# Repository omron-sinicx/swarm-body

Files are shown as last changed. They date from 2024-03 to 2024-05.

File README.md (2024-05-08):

# maru: a miniature-sized wheeled robot for swarm robotics research

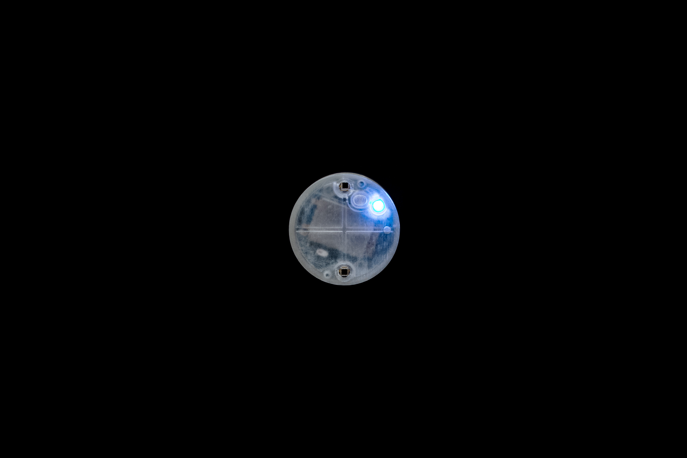
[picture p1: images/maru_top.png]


"maru" (= *miniature assemblage adaptive robot unit*) is a custom-made, miniature-sized, two-wheeled robot designed specifically for tabletop swarm robotics research.
This platform enables researchers and hobbyists to explore the dynamics of swarm robotics in a controlled, tabletop environment.

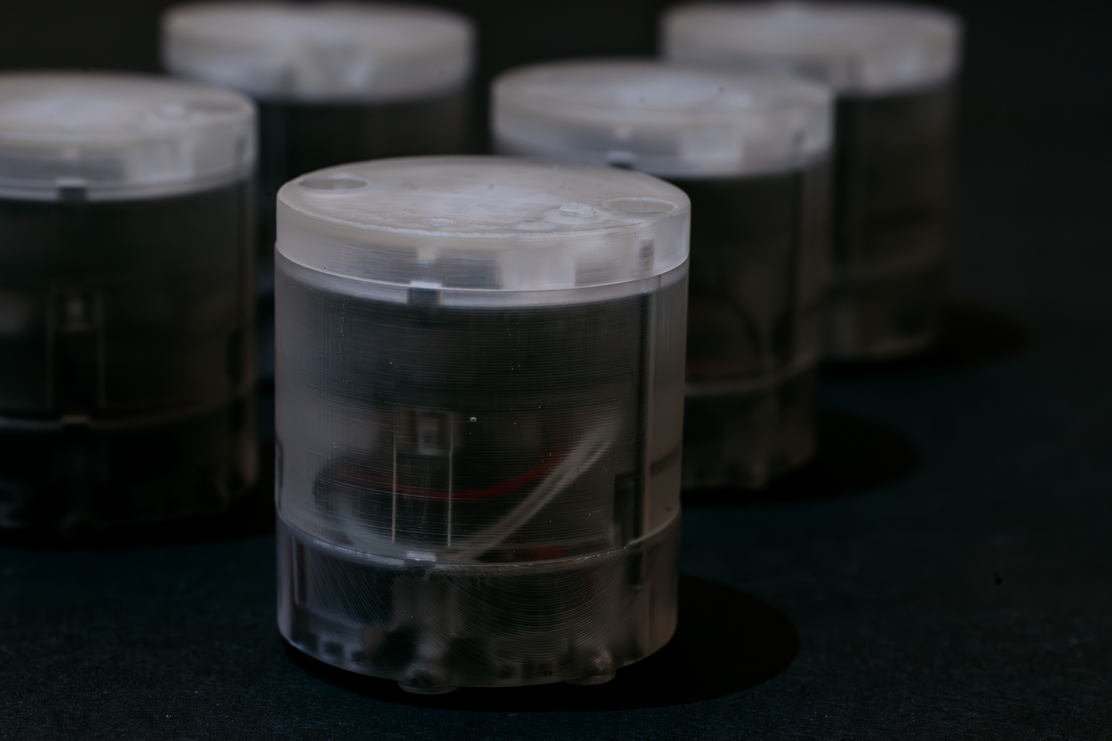
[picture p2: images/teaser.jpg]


This repository serves as a comprehensive resource for assembling and operating maru, providing detailed documentation and files, including:

- `hardware/3Dmodel` 3D models of the robot and its cradle (a combined communication and charging module),
- `hardware/circuit/schematic` Circuit schematics to guide the electronic assembly,
- `hardware/circuit/gerber` Gerber files for PCB manufacturing,
- `software/firmware` Firmware for both the robot and the cradle, distributed in binary format (Note: There are currently no plans to release the source code),
- `software/control` APIs and sample codes to help you get started with programming the robot for various tasks and behaviors (C# and Python).

This project draws inspiration from [Zooids](https://github.com/ShapeLab/SwarmUI), an open-source swarm robot platform.
Similar to Zooids, maru employs projection-based position tracking; however both maru's hardware and software are entirely new designs, another platform for swarm robotics research in HCI.

## Hardware
<!-- ![](./images/size.png) -->
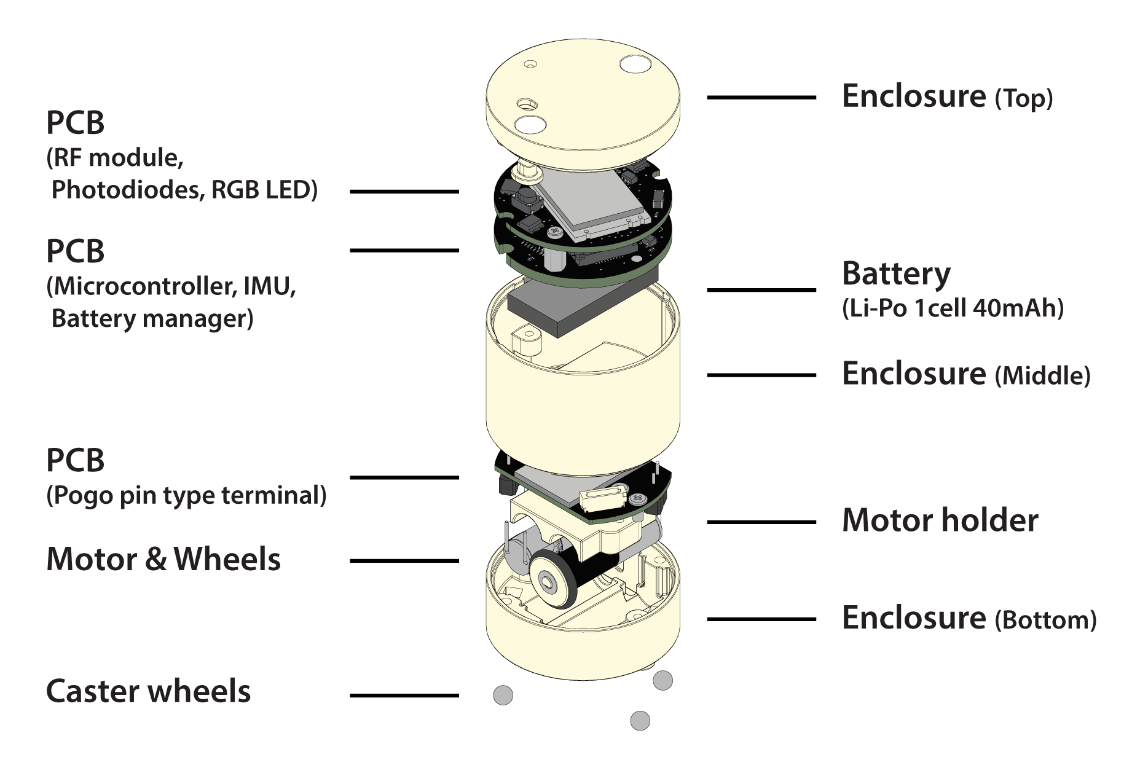
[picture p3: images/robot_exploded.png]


The hardware design is shown above.
The dimensions are 30 mm in diameter and 34 mm in height, weighing about 23 g.
The robot parts include a microcontroller unit (STM32G071KBU62 from STMicroelectronics), motor drivers (DRV8837DSGR3 from Texas Instruments), RF module (RF2401F204 from NiceRF), motors with a 26:1 planetary gearbox (Pololu 23575), photodiode (PD15-22C/TR86 from Everlight Electronics), and a 40mAh Li-Po battery.

Since the robot is lightweight, the robot may fall over while moving if the moving speed is too fast.
Magnets can be attached to the bottom of the robot, and the robot can be run on steel or other materials to keep it from falling over.

A detailed description of the hardware design and specifications is available [here](https://shigeodayo.notion.site/Hardware-Manual-8442a3ade0ba457dba1eb5f8b898ae2d?pvs=4).

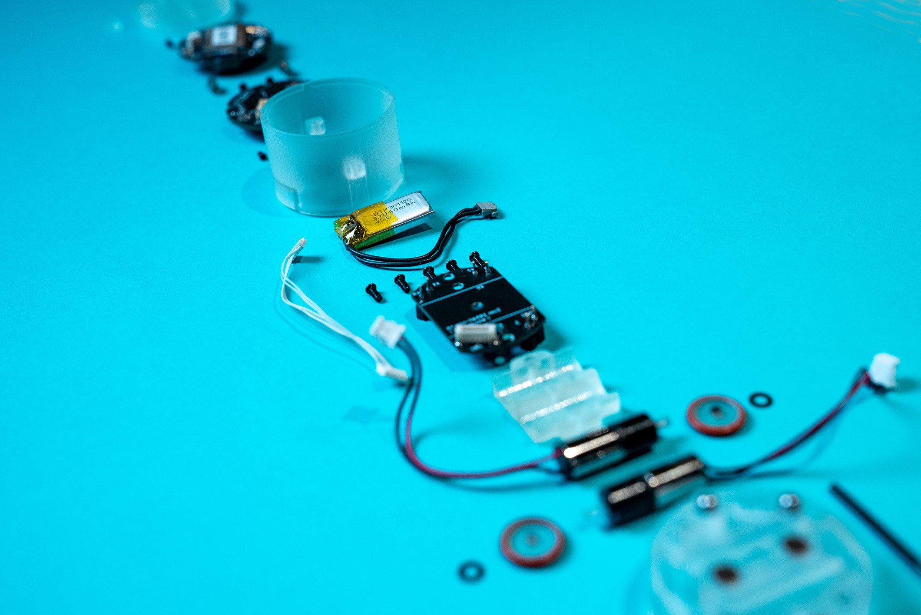
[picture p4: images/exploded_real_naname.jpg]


## Software

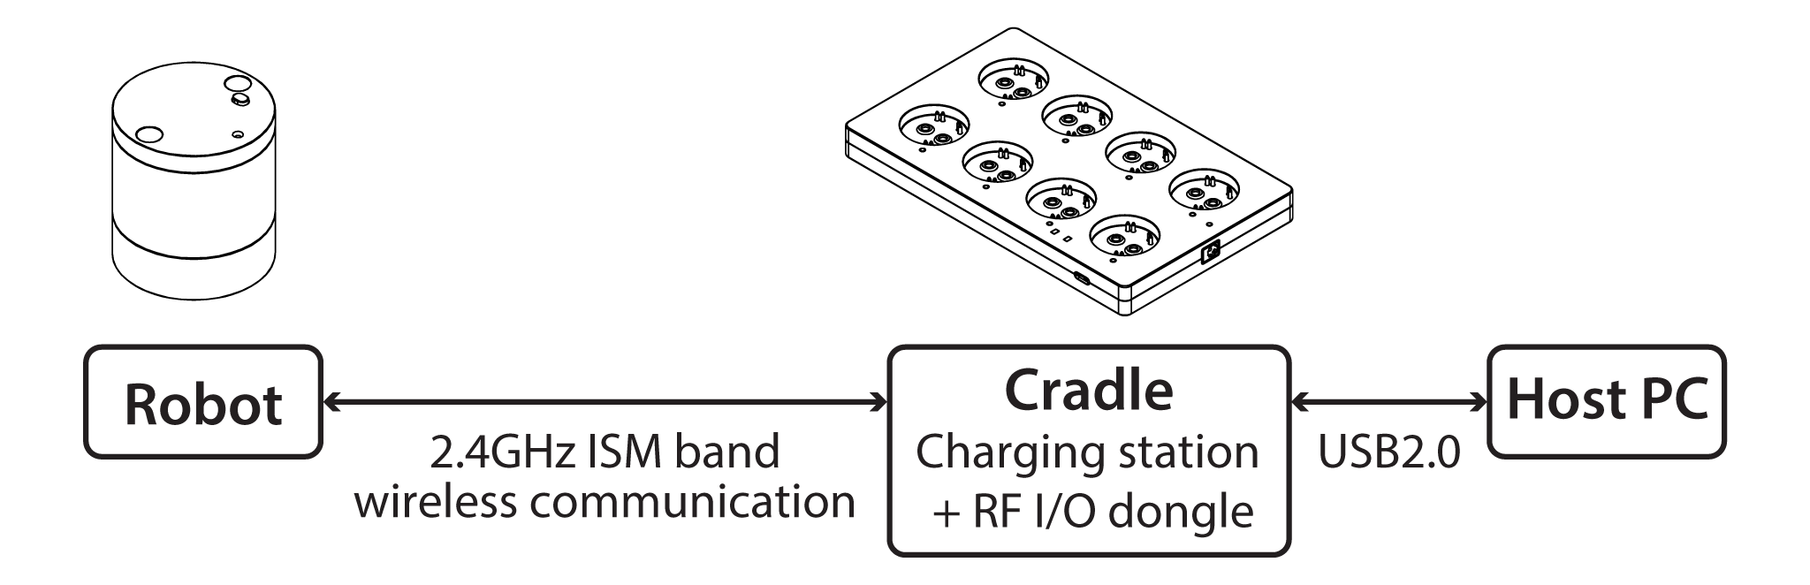
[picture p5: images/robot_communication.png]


The communication between the robots and the host computer is shown above.
The robots and the cradles (charging station + RF/IO dongle) are each equipped with an RF module and communicate through a 2.4GHz ISM band wireless communication.
The user does not need to be aware of the communication control between the robot and the cradles, as it is performed on the firmware of both devices.
The user can easily control the robot wirelessly by sending the specified commands.

A detailed description of the software design and specifications is available [here](https://shigeodayo.notion.site/Software-Manual-53adfd3b5a8c482b9a2acadc83991381?pvs=4).

## Projection-based Localization
A projection-based localization system used for the Zooids was used to track the robots.
A high-speed projector (DLP LightCrafter 45007 from Texas Instruments) was used to project a sequence of gray-coded patterns onto the table; the two photodiodes on the robot received the projected coded-pattern light, and the microcontroller of the robot decoded its pattern into position information.
Then, the robot calculated its orientation from the positions of two photodiodes and broadcasted its position and orientation information to the host computer.

For instructions on the projector tracking system, see https://github.com/ShapeLab/SwarmUI/tree/master/Hardware/Projector%20Tracking%20Setup

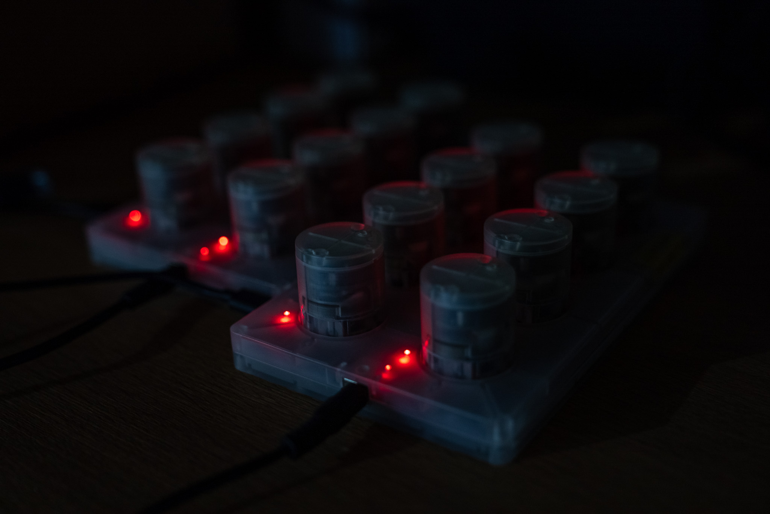
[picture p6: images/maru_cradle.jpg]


## Note

This is a joint work between [OMRON SINIC X Corporation](https://www.omron.com/sinicx/), [Cluster Metaverse Lab](https://lab.cluster.mu/en/), and [karakuri products, inc](https://krkrpro.com).

If you prefer purchasing pre-assembled robots instead of assembling them yourself, please contact [karakuri products, inc](https://krkrpro.com).

## Lisence

The software materials of this project are under an MIT license.

The hardware materials of this project are under a [Creative Commons Attribution 4.0 International License](https://creativecommons.org/licenses/by/4.0/).

## Paper
This robot was first introduced and used in the following paper:

Sosuke Ichihashi, So Kuroki, Mai Nishimura, Kazumi Kasaura, Takefumi Hiraki, Kazutoshi Tanaka, and Shigeo Yoshida. 2024. Swarm Body: Embodied Swarm Robots. In Proceedings of the CHI Conference on Human Factors in Computing Systems (CHI ’24), May 11–16, 2024, Honolulu, HI, USA. ACM, New York, NY, USA, 19 pages. https://doi.org/10.1145/3613904.3642870

```
@inproceedings{ichihashi2024swarm,
  author = {Ichihashi, Sosuke and Kuroki, So and Nishimura, Mai and Kasaura, Kazumi and Hiraki, Takefumi and Tanaka, Kazutoshi and Yoshida, Shigeo},
  title = {Swarm Body: Embodied Swarm Robots},
  year = {2024},
  publisher = {Association for Computing Machinery},
  address = {New York, NY, USA},
  url = {[https://doi.org/10.1145/3613904.3642870](https://doi.org/10.1145/3613904.3642870)},
  doi = {10.1145/3613904.3642870},
  booktitle = {Proceedings of the 2024 CHI Conference on Human Factors in Computing Systems},
  numpages = {19},
  location = {, Honolulu, HI, USA, },
  series = {CHI '24}
}
```

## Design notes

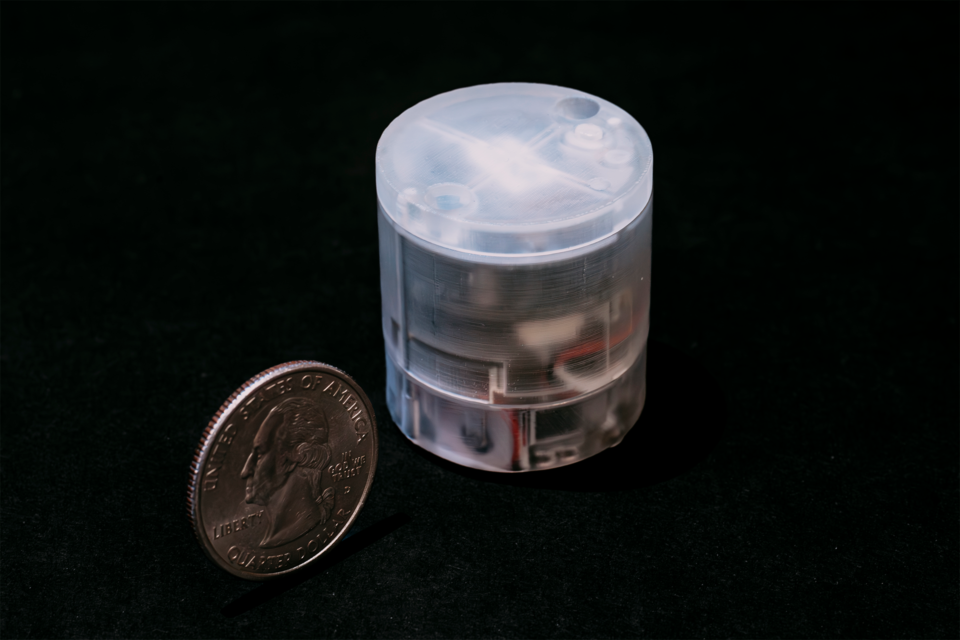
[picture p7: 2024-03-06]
images/size.png

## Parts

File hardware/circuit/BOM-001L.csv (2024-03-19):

Item | Quantity | Designator | Value | Description | Manufacturer | Manufacturer Part Number | Digikey Part Number
1 | 8 | C1, C2, C5, C15, C19, C20, C21, C37 | 0.1μF | CAP CER 0.1UF 10V X5R 0402 | Murata Electronics | GRM155R61A104KA01D | 490-1318-1-ND
2 | 3 | C3, C13, C14 | 1μF | CAP CER 1UF 10V X6S 0402 | Murata Electronics | GRM155C81A105KA12D | 490-12699-1-ND
3 | 1 | C4 | 0.47μF | CAP CER 0.47UF 10V X5R 0402 | Murata Electronics | GRM155R61A474KE15D | 490-3264-1-ND
4 | 4 | C6, C7, C8, C36 | 4.7μF | CAP CER 4.7UF 10V X5R 0402 | Murata Electronics | GRM155R61A475MEAAJ | 490-GRM155R61A475MEAAJCT-ND
5 | 1 | CN1 |  | CONN HDR 20POS SMD GOLD | Hirose Electric Co Ltd | DF17(2.0)-20DP-0.5V(57) | H11128CT-ND
6 | 1 | CN2 |  | CONN HEADER SMD R/A 3POS 1.3MM | JST Sales America Inc. | BM03B-ADHKS-GAN-ETB | 455-BM03B-ADHKS-GAN-ETBCT-ND
7 | 2 | CN3, CN5 |  | CONN HEADER SMD R/A 2POS 1.5MM | JST Sales America Inc. | S2B-ZR-SM4A-TF | 455-1693-1-ND
8 | 1 | CN4 |  | CONN HEADER SMD 6POS 0.8MM | JST Sales America Inc. | BM06B-SURS-TF | 455-3577-1-ND
9 | 1 | D1 |  | DIODE SCHOTT 100V 150MA SOD123F | Diotec Semiconductor | BAT46W | 4878-BAT46WCT-ND
10 | 1 | Q2 |  | MOSFET P-CH 20V 4.2A SOT23 | Diodes Incorporated | DMG2305UX-13 | DMG2305UX-13DICT-ND
11 | 2 | R2, R3 | 10Ω | RES SMD 10 OHM 1% 1/10W 0402 | Panasonic Electronic Components | ERJ-2RKF10R0X | P10.0LCT-ND
12 | 1 | R4 | 10kΩ | RES SMD 10K OHM 1% 1/10W 0402 | Panasonic Electronic Components | ERJ-2RKF1002X | P10.0KLCT-ND
13 | 1 | R5 | 100kΩ | RES SMD 100K OHM 1% 1/10W 0402 | Panasonic Electronic Components | ERJ-2RKF1003X | P100KLCT-ND
14 | 1 | U1 |  | IMU ACCEL/GYRO/COMPI2C/SPI 24QFN | TDK InvenSense | ICM-20948 | 1428-1123-1-ND
15 | 2 | U2, U3 |  | IC MOTOR DRIVER PAR 8WSON | Texas Instruments | DRV8837DSGR | 296-34806-1-ND
16 | 1 | U4 |  | IC BATT CNTL LI-ION 1CEL SOT23-5 | Microchip Technology | MCP73831T-2ACI/OT | MCP73831T-2ACI/OTCT-ND
17 | 1 | U5 |  | IC REG LINEAR 1.8V 50MA SC70-5 | Texas Instruments | TPS79718DCKR | 296-11988-1-ND
18 | 1 | U9 |  | IC TRANSLATOR BIDIR 16TSSOP | Texas Instruments | TXB0106PWR | 296-23759-1-ND
19 | 1 | U10 |  | IC OR CTRLR SRC SELECT TSOT23-6 | Analog Devices Inc. | LTC4412IS6#TRPBF | 505-LTC4412IS6#TRPBFCT-ND
20 | 1 | U11 |  | IC MCU 32BIT 128KB FLSH 32UFQFPN | STMicroelectronics | STM32G071KBU6 | 497-18357-ND

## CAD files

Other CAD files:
hardware/3Dmodel/cradle/CATIA/cradle_Assembly1.CATProduct
hardware/3Dmodel/cradle/CATIA/cradle_Assembly1/01080537_NBR_sheet_t1mm_18x12.CATPart
hardware/3Dmodel/cradle/CATIA/cradle_Assembly1/AD-B90P130.CATPart
hardware/3Dmodel/cradle/CATIA/cradle_Assembly1/ASB-1405E.CATPart
hardware/3Dmodel/cradle/CATIA/cradle_Assembly1/BLMJ3.CATPart
hardware/3Dmodel/cradle/CATIA/cradle_Assembly1/DTP301120.CATPart
hardware/3Dmodel/cradle/CATIA/cradle_Assembly1/F-0250EB-02.CATPart
hardware/3Dmodel/cradle/CATIA/cradle_Assembly1/F-1430EB-03.CATPart
hardware/3Dmodel/cradle/CATIA/cradle_Assembly1/F-1735EB-02.CATPart
hardware/3Dmodel/cradle/CATIA/cradle_Assembly1/F-1745EB-02.CATPart
hardware/3Dmodel/cradle/CATIA/cradle_Assembly1/LL-2104-01.CATPart
hardware/3Dmodel/cradle/CATIA/cradle_Assembly1/ND0051.CATPart
hardware/3Dmodel/cradle/CATIA/cradle_Assembly1/NSB7_ext_0.10.CATPart
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

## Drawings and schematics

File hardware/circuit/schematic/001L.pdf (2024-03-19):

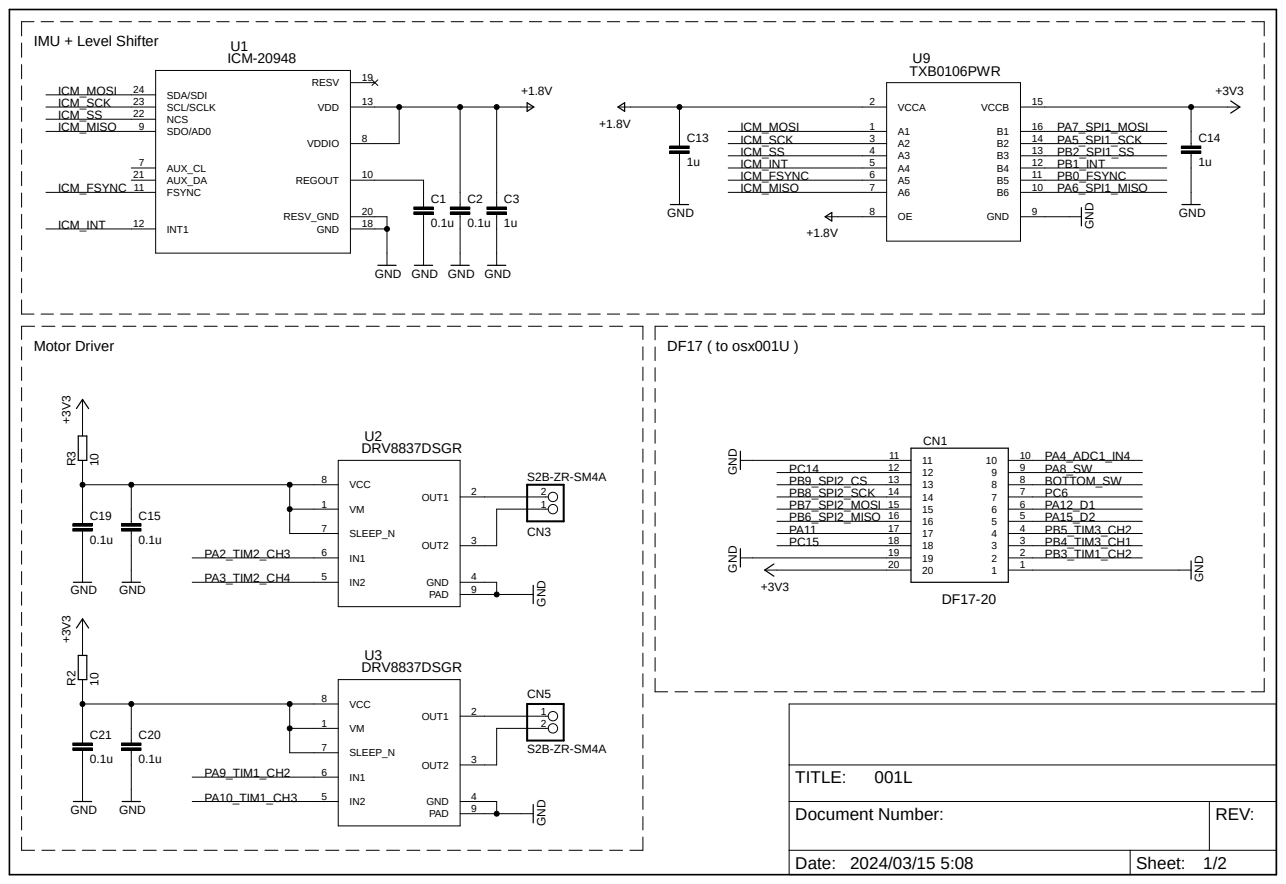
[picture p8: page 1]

GND GND

Document Number: | REV:

Date: 2024/03/15 5:08 | Sheet: 1/2

# GND BAT46W ⁺⁵V

# C8 D¹

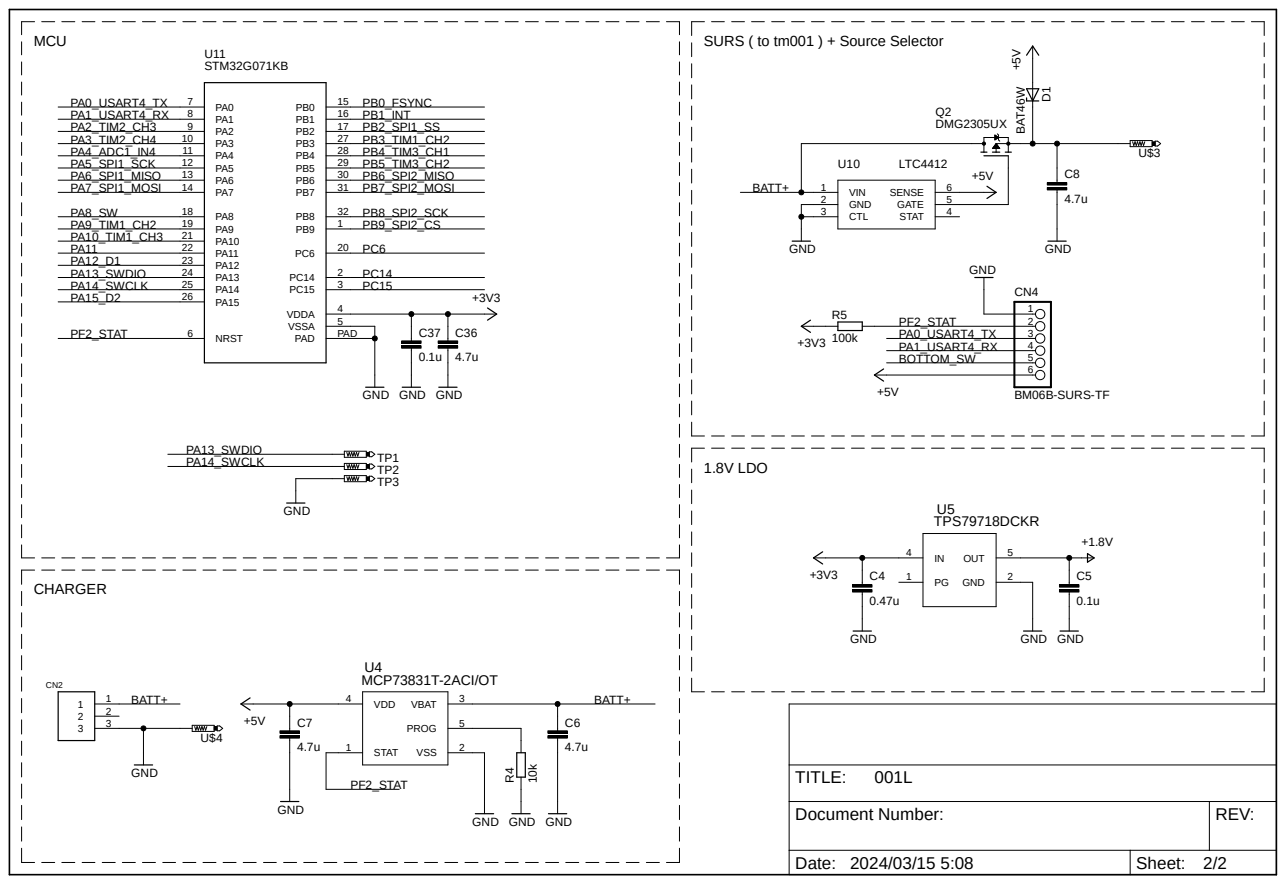
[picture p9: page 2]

Document Number: | REV:

Date: 2024/03/15 5:08 | Sheet: 2/2

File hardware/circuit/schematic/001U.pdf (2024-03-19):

# +3V3 GND

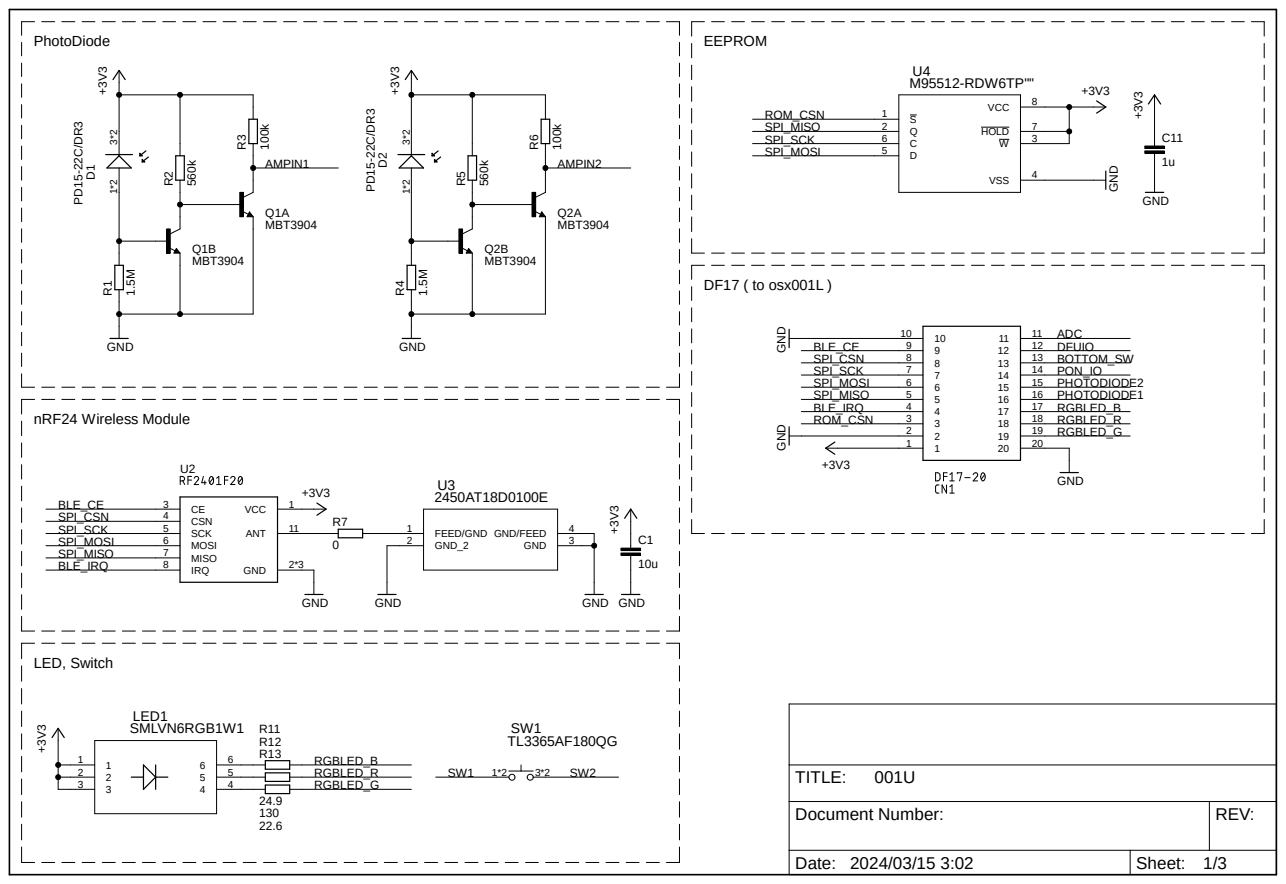
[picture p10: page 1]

Document Number: | REV:

Date: 2024/03/15 3:02 | Sheet: 1/3

# GND ⁺³V³

# GND ⁺³V³

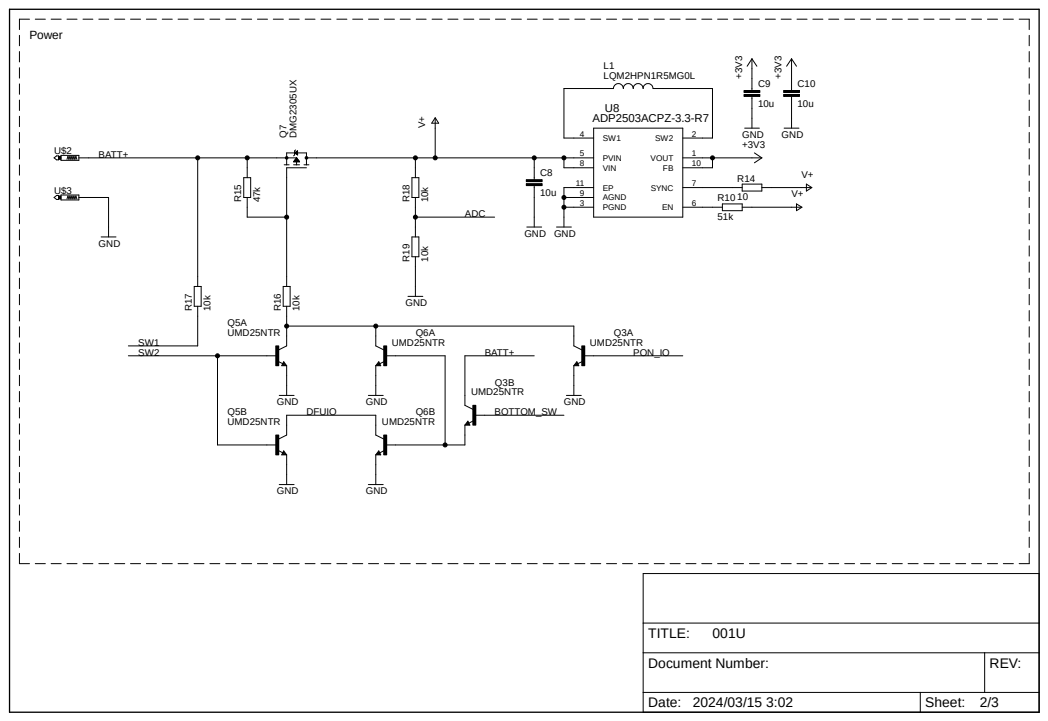
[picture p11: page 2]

Document Number: | REV:

Date: 2024/03/15 3:02 | Sheet: 2/3

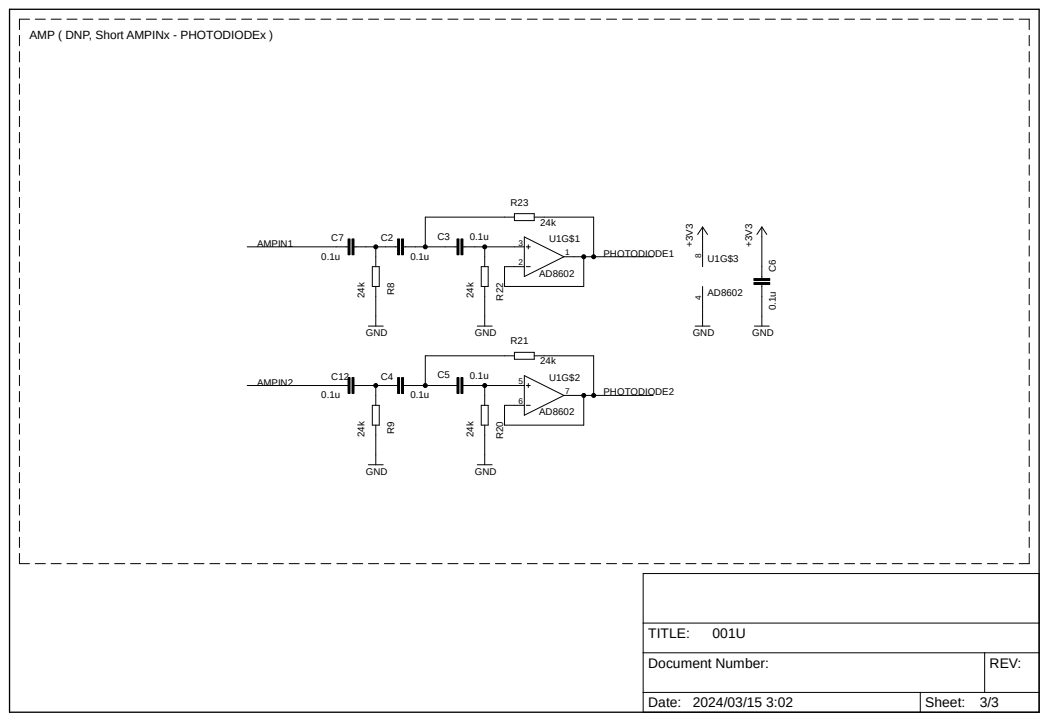
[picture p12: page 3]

AMP ( DNP, Short AMPINx - PHOTODIODEx )

Document Number: | REV:

Date: 2024/03/15 3:02 | Sheet: 3/3

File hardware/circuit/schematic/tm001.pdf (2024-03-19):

# BM06B-SURS-TF GND

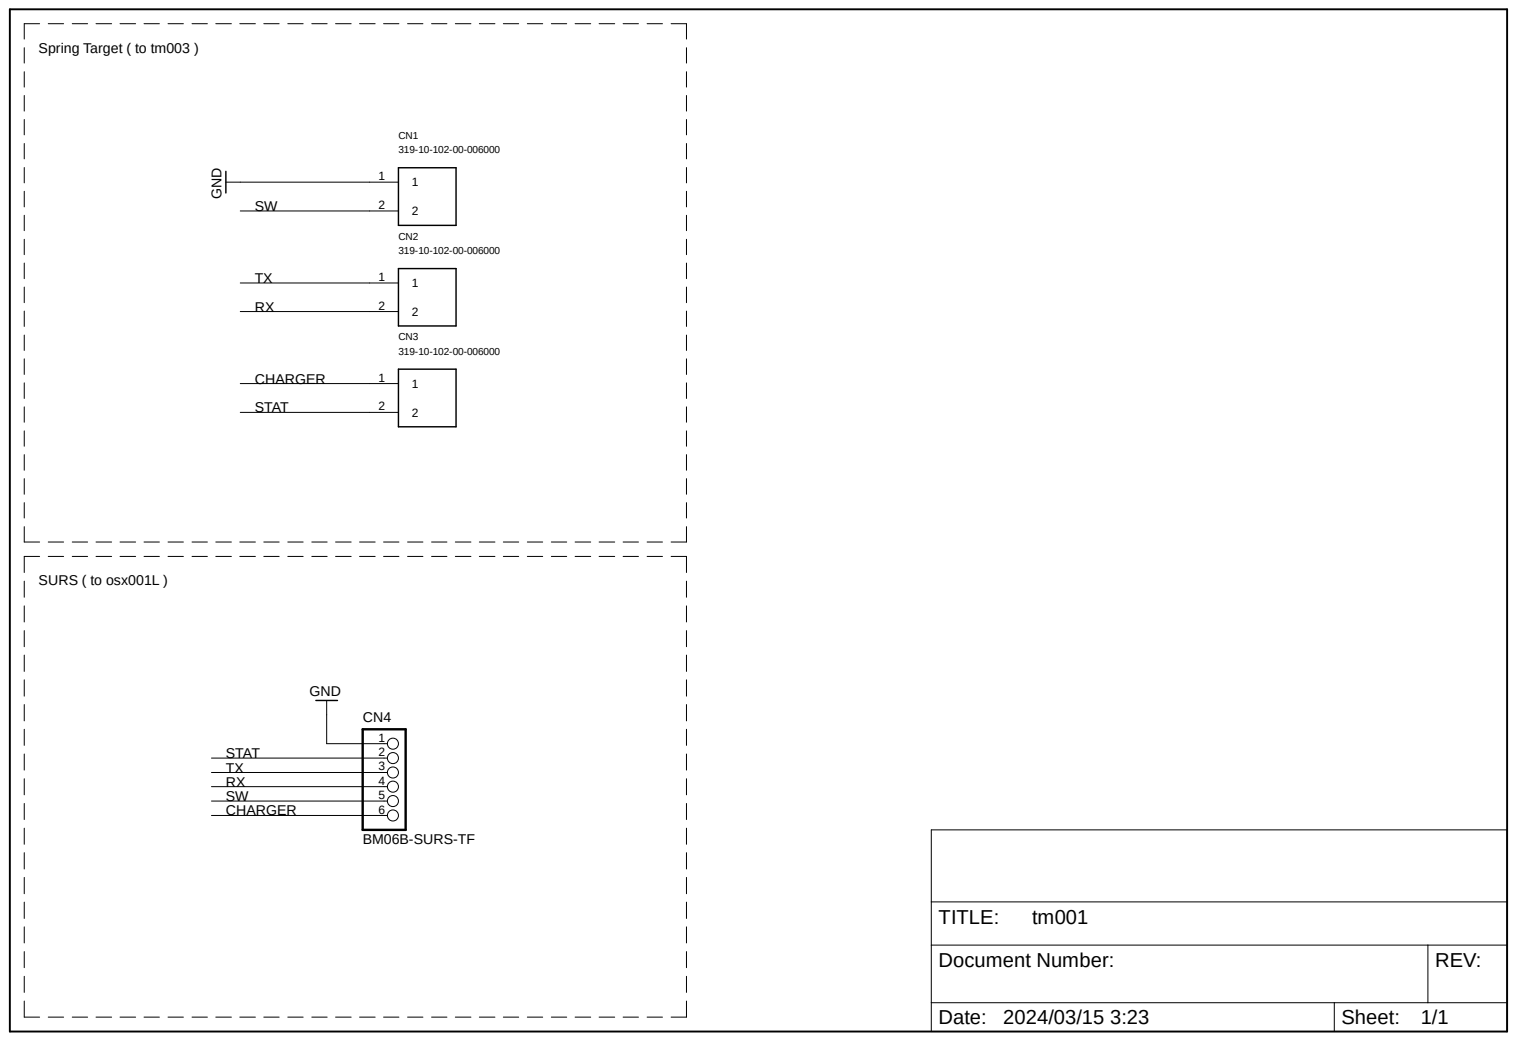
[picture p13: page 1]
SURS ( to osx001L ); GND; STAT; CHARGER; TITLE:

Spring Target ( to tm003 )

Document Number: | REV:

Date: 2024/03/15 3:23 | Sheet: 1/1

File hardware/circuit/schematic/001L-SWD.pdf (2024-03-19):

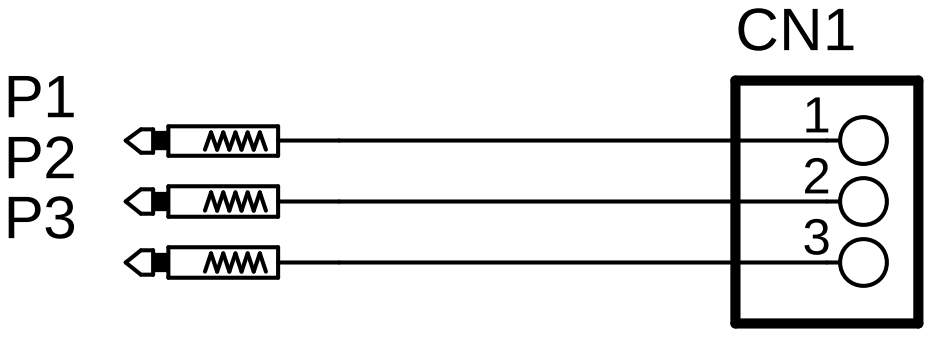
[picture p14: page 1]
TITLE:; 001L-SWD

Document Number: | REV:

Date: 2024/03/15 1:45 | Sheet: 1/1

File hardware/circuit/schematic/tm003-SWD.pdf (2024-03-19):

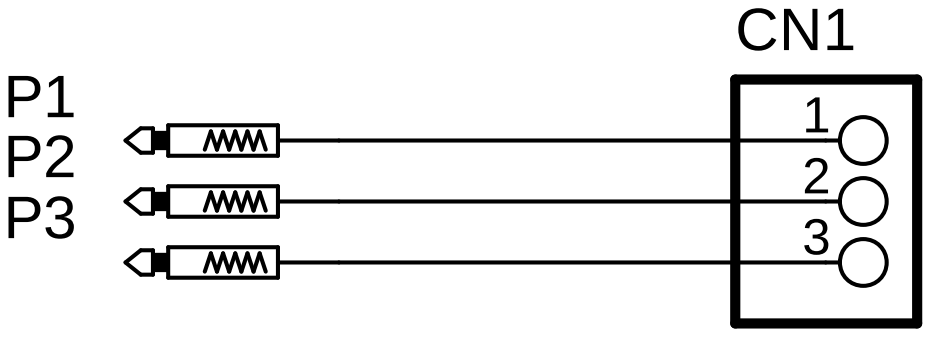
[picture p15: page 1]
TITLE:; tm003-SWD

Document Number: | REV:

Date: 2024/03/15 6:54 | Sheet: 1/1

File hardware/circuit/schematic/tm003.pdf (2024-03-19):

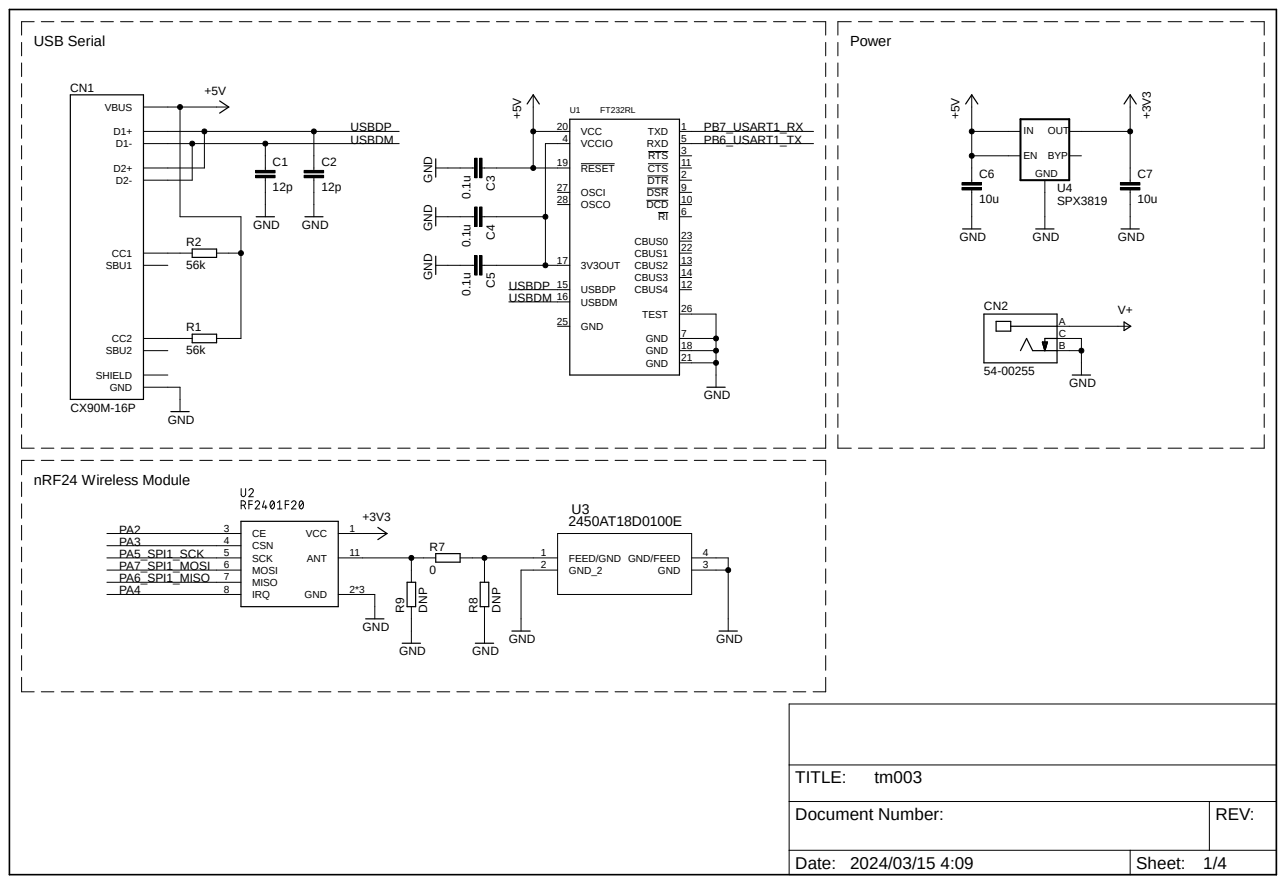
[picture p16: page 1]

Document Number: | REV:

Date: 2024/03/15 4:09 | Sheet: 1/4

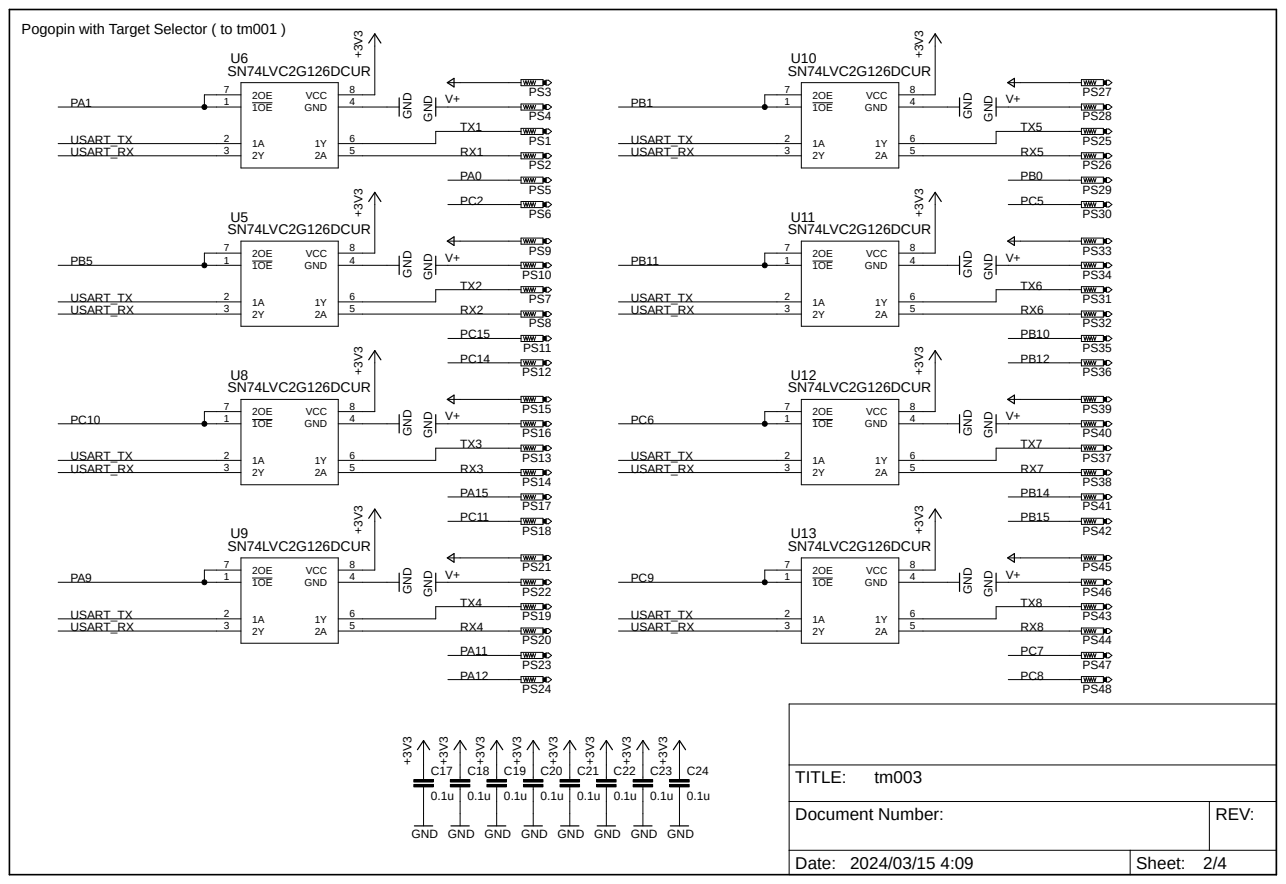
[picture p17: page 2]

Document Number: | REV:

Date: 2024/03/15 4:09 | Sheet: 2/4

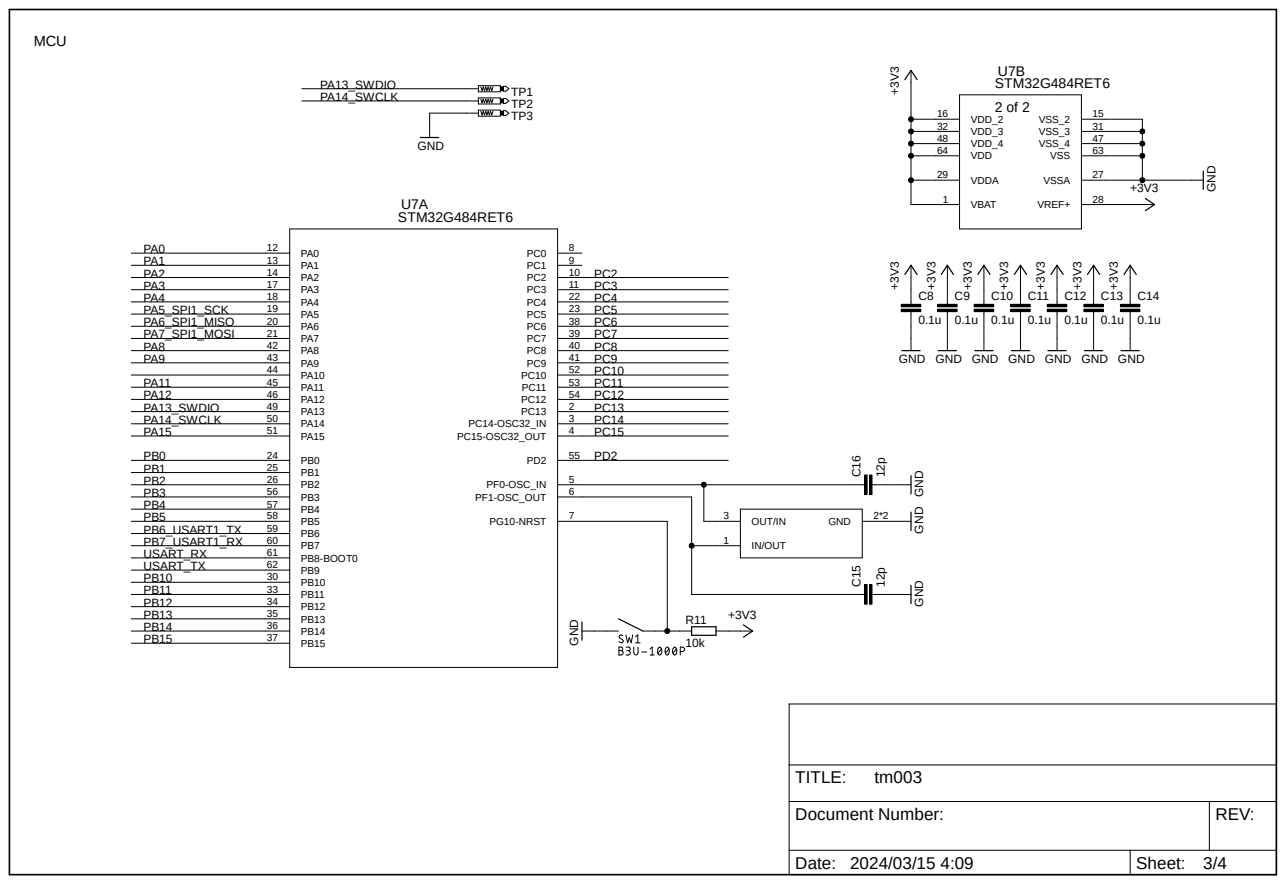
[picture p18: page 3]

Document Number: | REV:

Date: 2024/03/15 4:09 | Sheet: 3/4

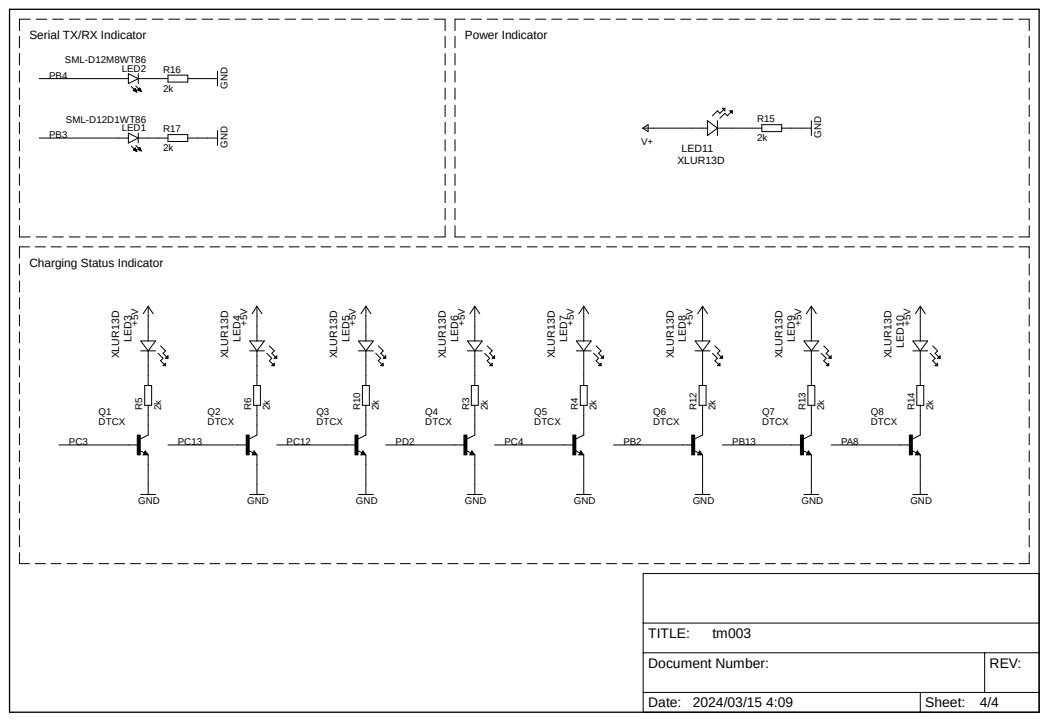
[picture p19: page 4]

Serial TX/RX Indicator

Document Number: | REV:

Date: 2024/03/15 4:09 | Sheet: 4/4

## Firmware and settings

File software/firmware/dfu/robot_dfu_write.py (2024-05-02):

#! /usr/bin/env python3
# encoding: utf-8

import sys
import serial
from serial.tools import list_ports
from time import sleep

pageSize = 2048
keyCode = bytes([0xFF, 0xFD, 0x02, 0x00, 0xFA, 0xF8])

def calculateCheckSum(array):
    sum = 0
    for data in array:
        sum += data
    return sum & 0xFF

def main():
    args = sys.argv

    # Exit if no serial port and binary file specified
    if len(args) < 4:
        ports = list_ports.comports()
        devices = [info.device for info in ports]
        print("Specify serial port and binary file\r\n")
        print("e.g., python robot_dfu_write.py COM3 firmware.bin 0\r\n")
        print("Port List : \r\n")
        for port in ports:
            print(port)
        sys.exit(0)

    # Firmware loading
    f = open(args[2], 'rb')
    flashBuffer = f.read()
    fileSize = len(flashBuffer)
    pageNum = int(fileSize / pageSize)
    if fileSize % pageSize != 0:
        pageNum = pageNum + 1
    writtenPage = 0

    # Preparing the serial port
    port = serial.Serial(args[1], 1000000, timeout=1)

    # Selecting the port
    setDFUTarget = [0xFF, 0xFD, 0x03, 0x00, 0xF6, int(args[3])]
    setDFUTarget.append(calculateCheckSum(setDFUTarget))
    port.write(setDFUTarget)

    # Switching the robot to DFU mode
    rebootBoard = [0xFF, 0xFD, 0x03, 0x00, 0x01, 1]
    rebootBoard.append(calculateCheckSum(rebootBoard))
    port.write(rebootBoard)

    receiveState = 0
    receiveFlag = 0

    while(True):
        # Waiting for request command reception
        rcvArray = port.read_all()

        for data in rcvArray:
            if data == keyCode[receiveState]:
                receiveState = receiveState + 1
            else:
                receiveState = 0

            if receiveState == 4:
                receiveState = 0
                receiveFlag = 1

        if receiveFlag == 0:
            continue

        receiveFlag = 0

        # Firmware writing
        # Header
        flashData = bytes([0xFF, 0xFD])
        flashArray = bytearray(flashData)

        # LEN_L, LEN_H
        pageLength = pageSize
        if fileSize - pageSize * writtenPage < pageSize:
            pageLength = fileSize - pageSize * writtenPage

        flashArray.append((pageLength + 2) & 0xFF)
        flashArray.append((pageLength + 2) >> 8)

        # Instruction
        if writtenPage < pageNum - 1:
            flashArray.append(0xFC)
        else:
            flashArray.append(0xFD)

        # Copy Parameters
        for num in range(pageLength):
            flashArray.append(flashBuffer[writtenPage * pageSize + num])

        # Check-Sum
        flashArray.append(calculateCheckSum(flashArray))
        flashData = bytes(flashArray)

        # Send Firmware
        port.write(flashData)

        writtenPage = writtenPage + 1

        print((int)(writtenPage / pageNum * 100), end='')
        print("% Complete...")
        if writtenPage == pageNum:
            sleep(1)
            # Switching to normal mode
            setDFUTarget = [0xFF, 0xFD, 0x03, 0x00, 0xF6, 8]
            setDFUTarget.append(calculateCheckSum(setDFUTarget))
            port.write(setDFUTarget)
            break

if __name__ == '__main__':
    main()

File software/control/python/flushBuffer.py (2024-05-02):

import sys
from maru import osx001Driver
from serial.tools import list_ports

def main():
    args = sys.argv

    # Exit if no serial port specified
    if len(args) < 2:
        ports = list_ports.comports()
        devices = [info.device for info in ports]
        print("Specify serial port\r\n")
        print("e.g., python shutdownAllRobot.py COM3\r\n")
        print("Port List : \r\n")
        for port in ports:
            print(port)
        sys.exit(0)

    # Initialization
    driver = osx001Driver(args[1])

    driver.flushBuffer()

if __name__ == '__main__':
    main()

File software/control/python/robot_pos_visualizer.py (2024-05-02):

import numpy as np
import matplotlib.pyplot as plt
from matplotlib.animation import FuncAnimation
import threading
import random
import time

from maru import osx001Driver
from serial.tools import list_ports

# The acquisition of information from robots may be delayed because the amount of communication increases as the number of robots increases. There is a problem with the smooth acquisition of location information for robots with more than four units in a Windows environment. No problem on Mac and Ubuntu (probably an OS-derived Thread implementation issue).

# maximum number of robots
robt_num = 12

# Enumerate the port names of the connected cradle
# ports = ["COM3", "COM2"]
ports = ["/dev/cu.usbserial-AR0KBALD", "/dev/cu.usbserial-AR0KBALC"]

# Initial robot positions.
positions = np.full((robt_num, 2), [450, 300], dtype=np.float64)

drivers = []
for i in range(len(ports)):
    driver = osx001Driver(ports[i])
    drivers.append(driver)


fig, ax = plt.subplots()
sc = ax.scatter(positions[:, 0], positions[:, 1])

ax.set_xlim(-450, 450)
ax.set_ylim(-300, 300)

def update(frame):
    sc.set_offsets(positions)
    return sc,

def fetch_data():

    while True:
        for i in range(len(drivers)):
            driver = drivers[i]

            data_dict = driver.checkStatusPacket()

            if data_dict is not None:
                for id in data_dict:
                    positions[id-1, 0] = data_dict[id][0]
                    positions[id-1, 1] = data_dict[id][1]

        # time.sleep(0.1)  # delay

thread = threading.Thread(target=fetch_data)
thread.daemon = True
thread.start()

ani = FuncAnimation(fig, update, interval=100)  # Updated every 100 milliseconds

plt.show()
